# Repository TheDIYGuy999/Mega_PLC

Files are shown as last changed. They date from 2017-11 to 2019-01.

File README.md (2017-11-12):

# This is an Arduino based, modular Industrial PLC

## I have designed this PLC back in 2016. It is currently in use in an industrial screw tightening robot:
- 4 stepper motors for X, Y, Z axes and for screw tightening
- Matrix keyboard
- I2C LCD
- Digital I/O in use for pneumatic screw feeding system, buttons and reference switches

## Features:
- Works wit an Arduino MEGA or DUE
- DO board with 16 24V, 500mA PNP digital outputs, optoinsulated, short circuit protected @ about 900mA
- DI board with 16 24V PNP digital inputs, optoinsulated
- Stepper board for 4 stepper motors, torque adjustable via PWM
- Slot for communication board (I2C, CAN, SPI, 2x Serial)
- Slot for analog board (Analog in, PWM, DAC, I2C)

## This repo contains:
- Eagle schematics
- Eagle board files
- PDF schematics
- The analog and communication boards were made out of perfboard and are NOT included. Maybe someone other is interested in adding them.

## Pictures:
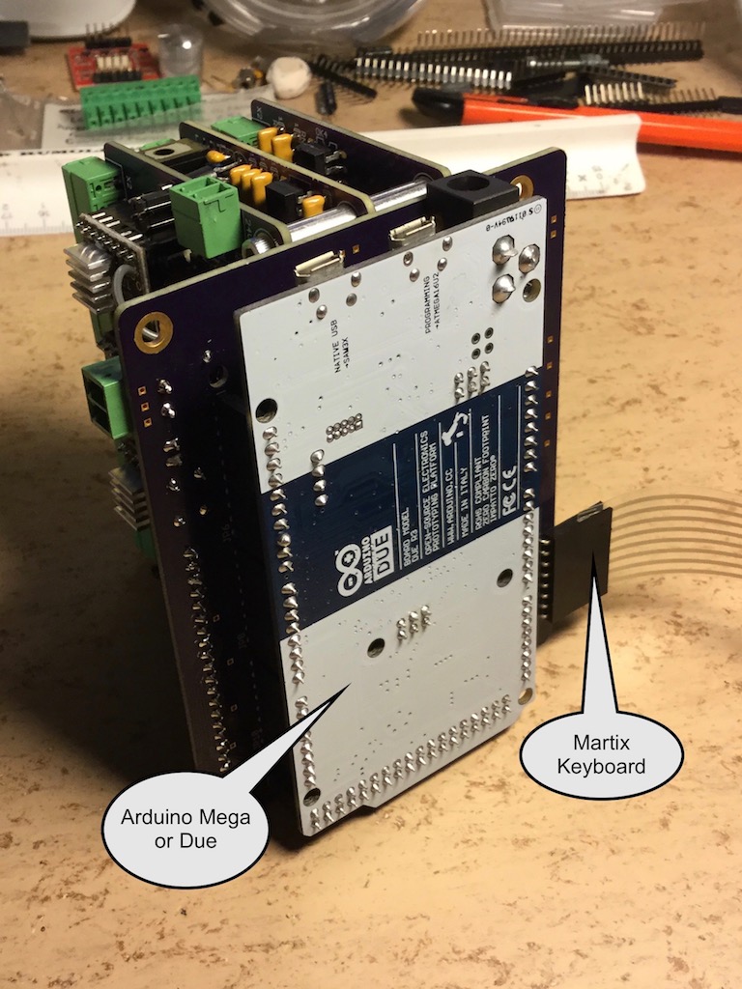
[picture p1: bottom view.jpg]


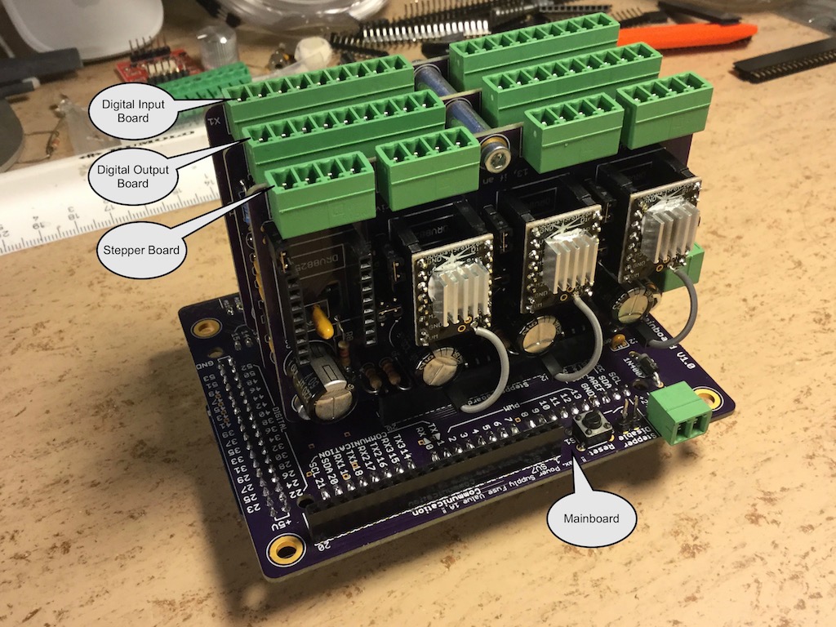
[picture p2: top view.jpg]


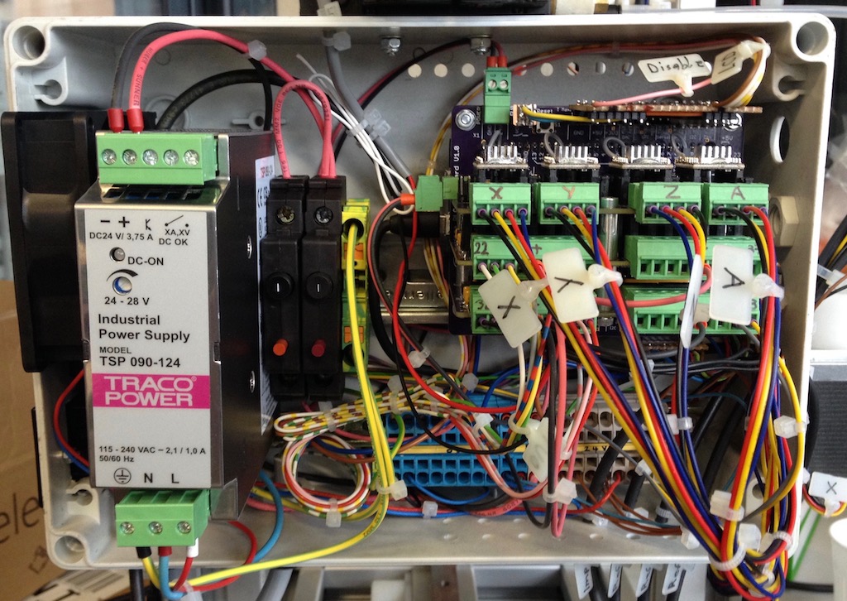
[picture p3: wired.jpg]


## Videos:
- I/O boards: https://www.youtube.com/watch?v=W2pYYh6aUXc
- First tepper tests: https://www.youtube.com/watch?v=gJDdZBuH5Kc

(c) 2016  TheDIYGuy999

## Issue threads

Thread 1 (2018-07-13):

Thyristor BT169 in Digital Output Circuit

rjtphate7, 2018-07-13:
Hey TheDIYGuy999,
The purpose of thyristor BT169 in digital output circuit is quite unclear to me, can you explain?
I have simulated and found it ON irrespective of input to optocoupler

TheDIYGuy999, 2018-07-14:
It does the output short circuit protection, which is triggered at about 0.9A.
The nominal output current is 0.5A

rjtphate7, 2018-07-16:
Any suggestions in case I wish to increase the nominal output current to 2 A?

TheDIYGuy999, 2018-07-16:
0.5A is standard for PLC digital outputs. If you want more, I recommend to use a relay, which is controlled by the PLC output.

rjtphate7, 2018-07-17:
**Thanks for the suggestion**

Closed 2018-07-17.

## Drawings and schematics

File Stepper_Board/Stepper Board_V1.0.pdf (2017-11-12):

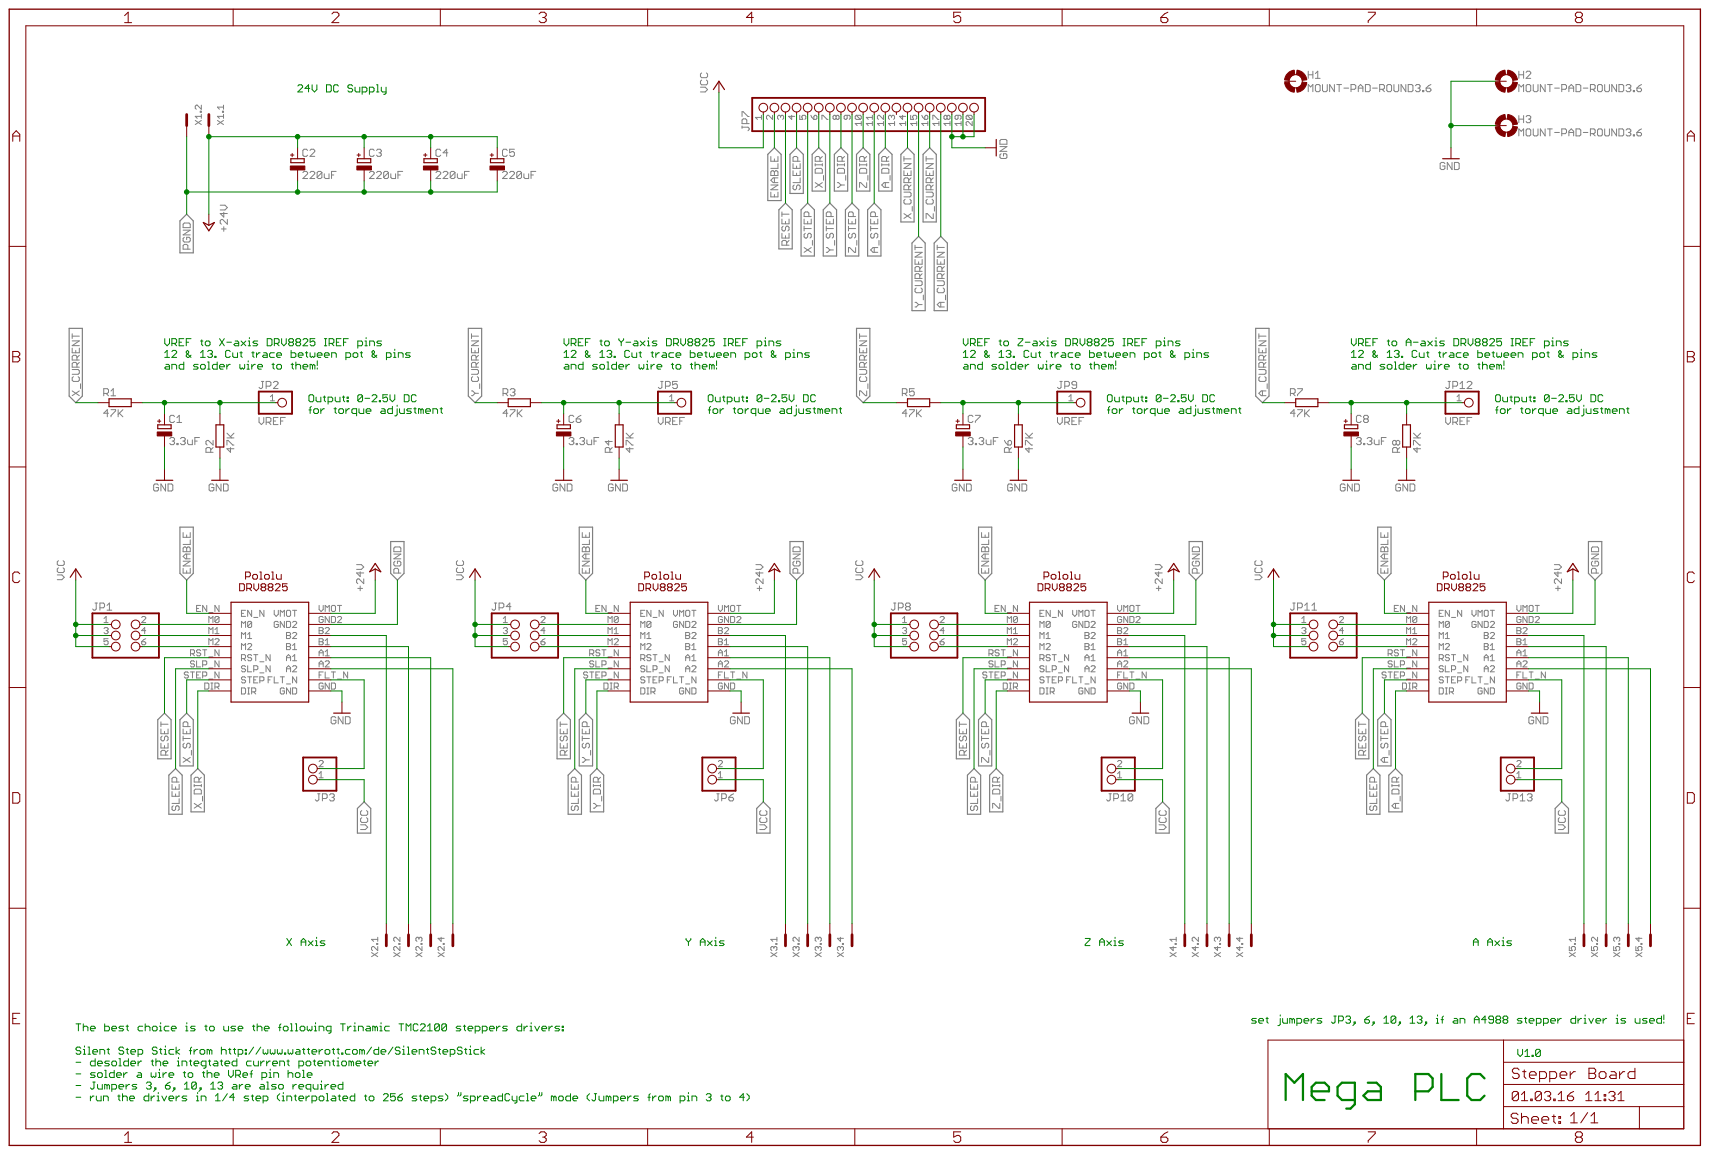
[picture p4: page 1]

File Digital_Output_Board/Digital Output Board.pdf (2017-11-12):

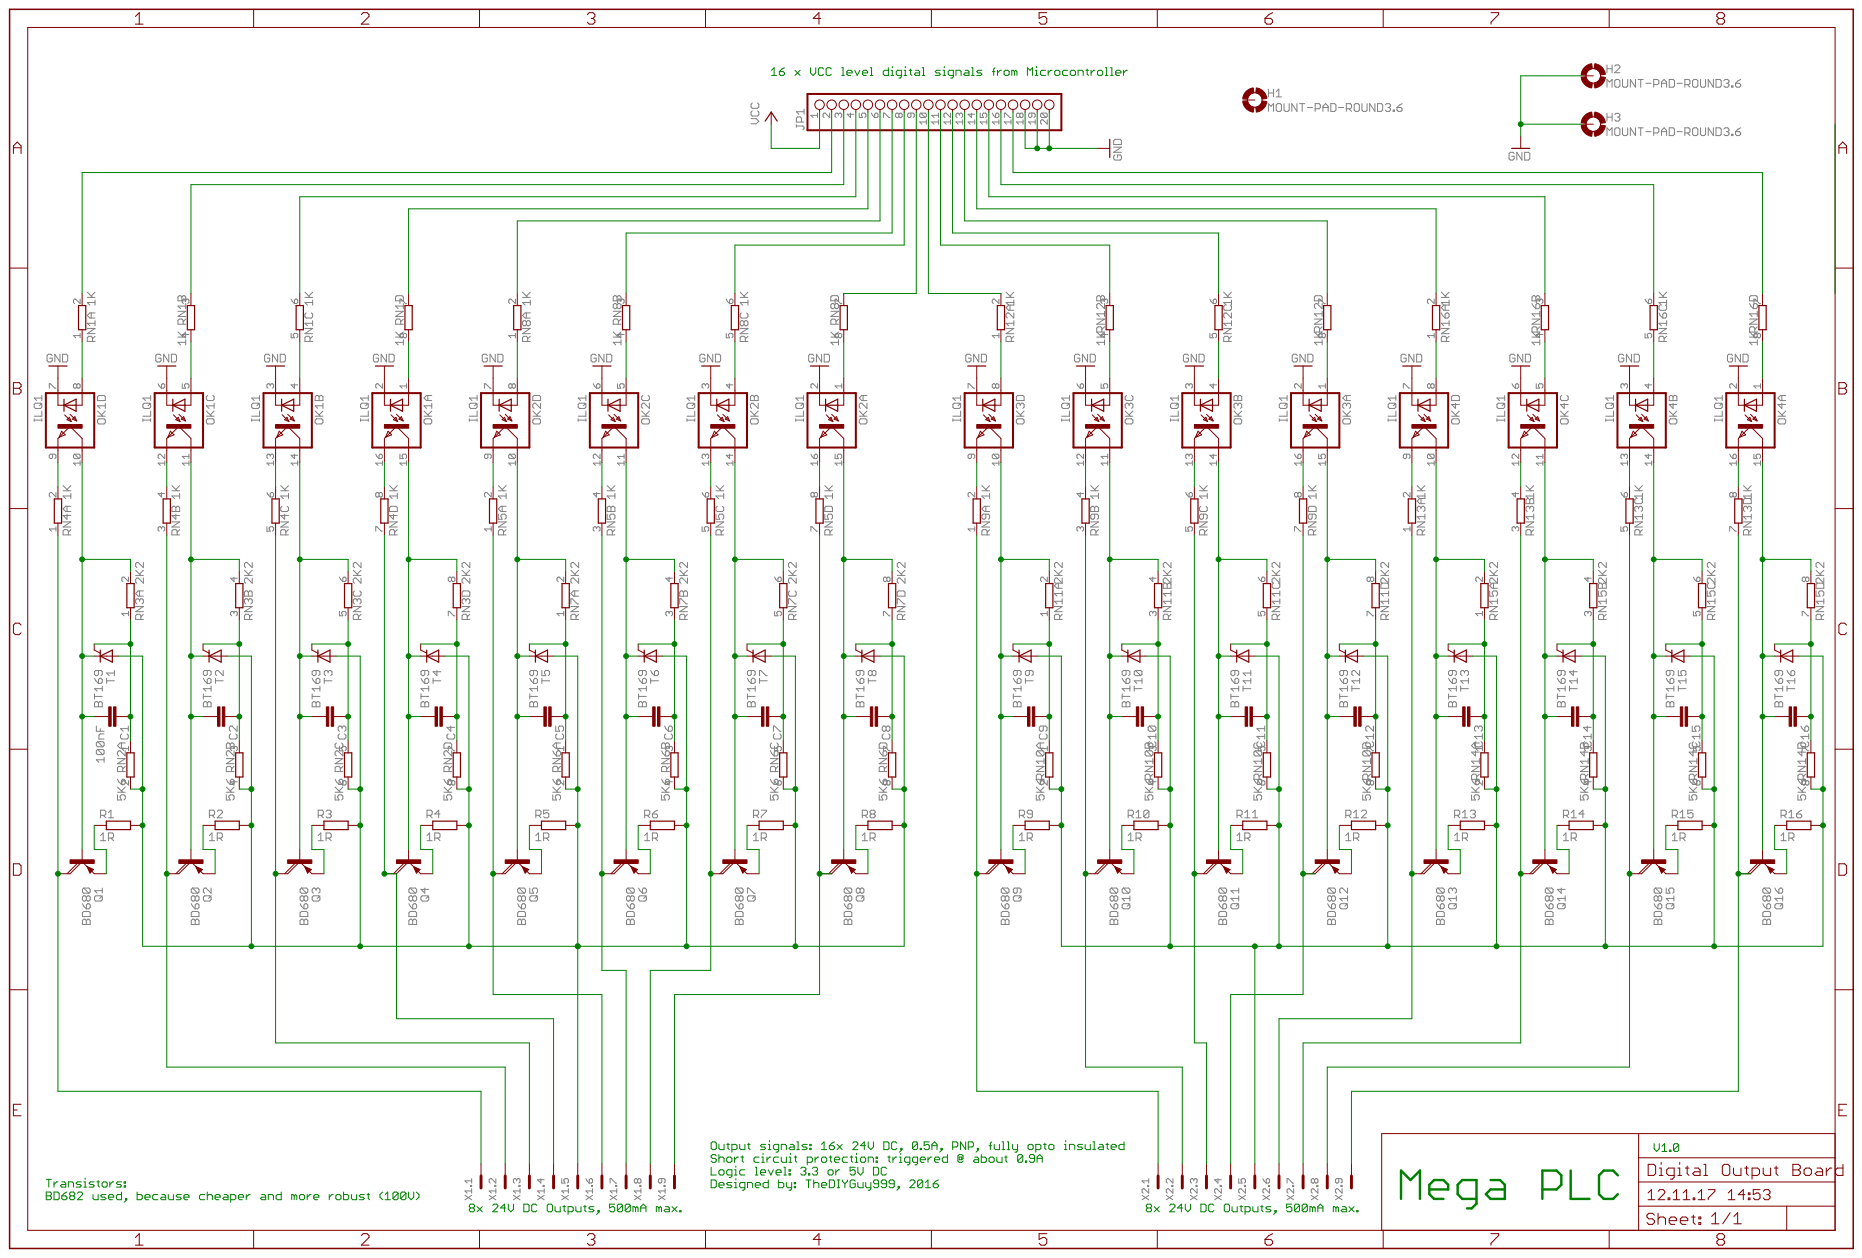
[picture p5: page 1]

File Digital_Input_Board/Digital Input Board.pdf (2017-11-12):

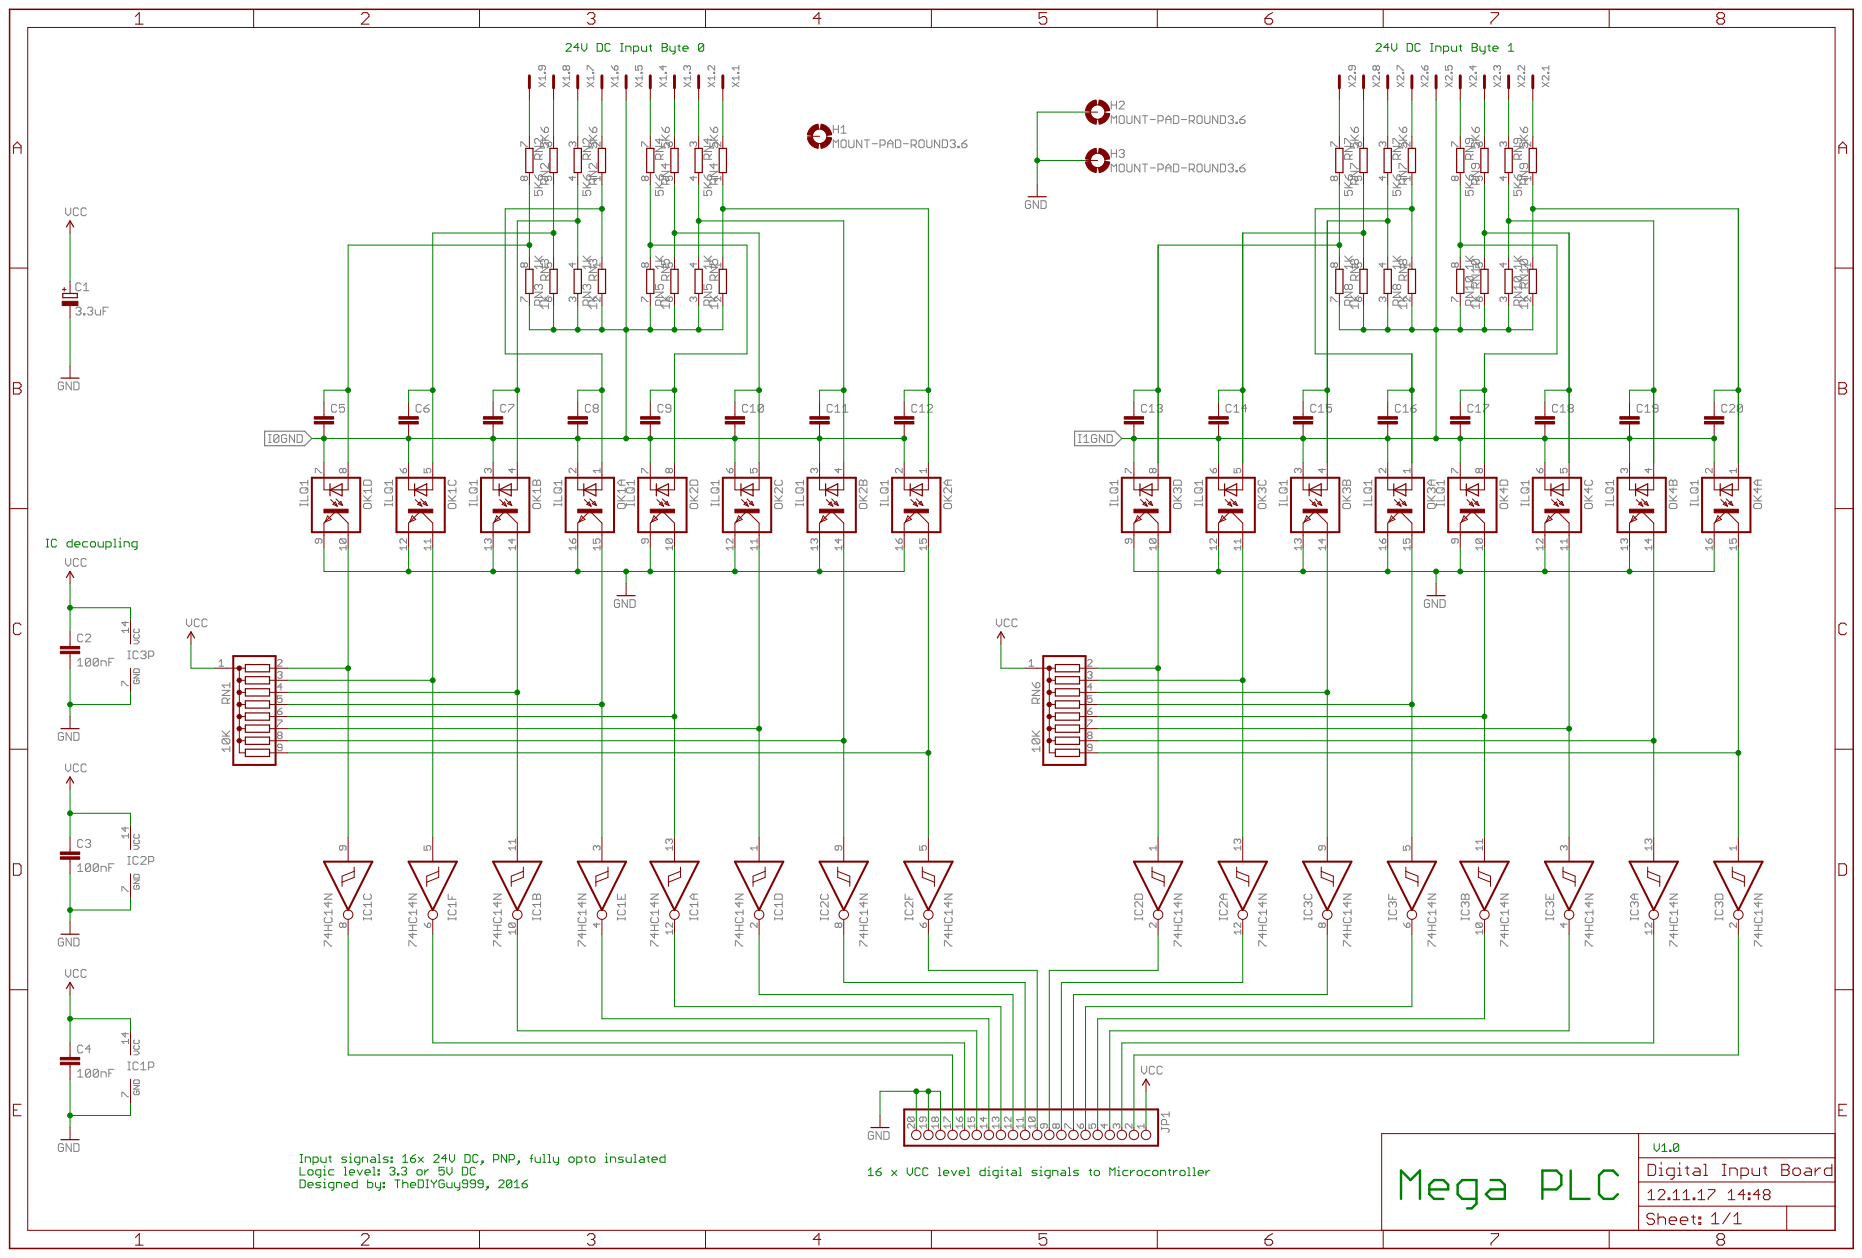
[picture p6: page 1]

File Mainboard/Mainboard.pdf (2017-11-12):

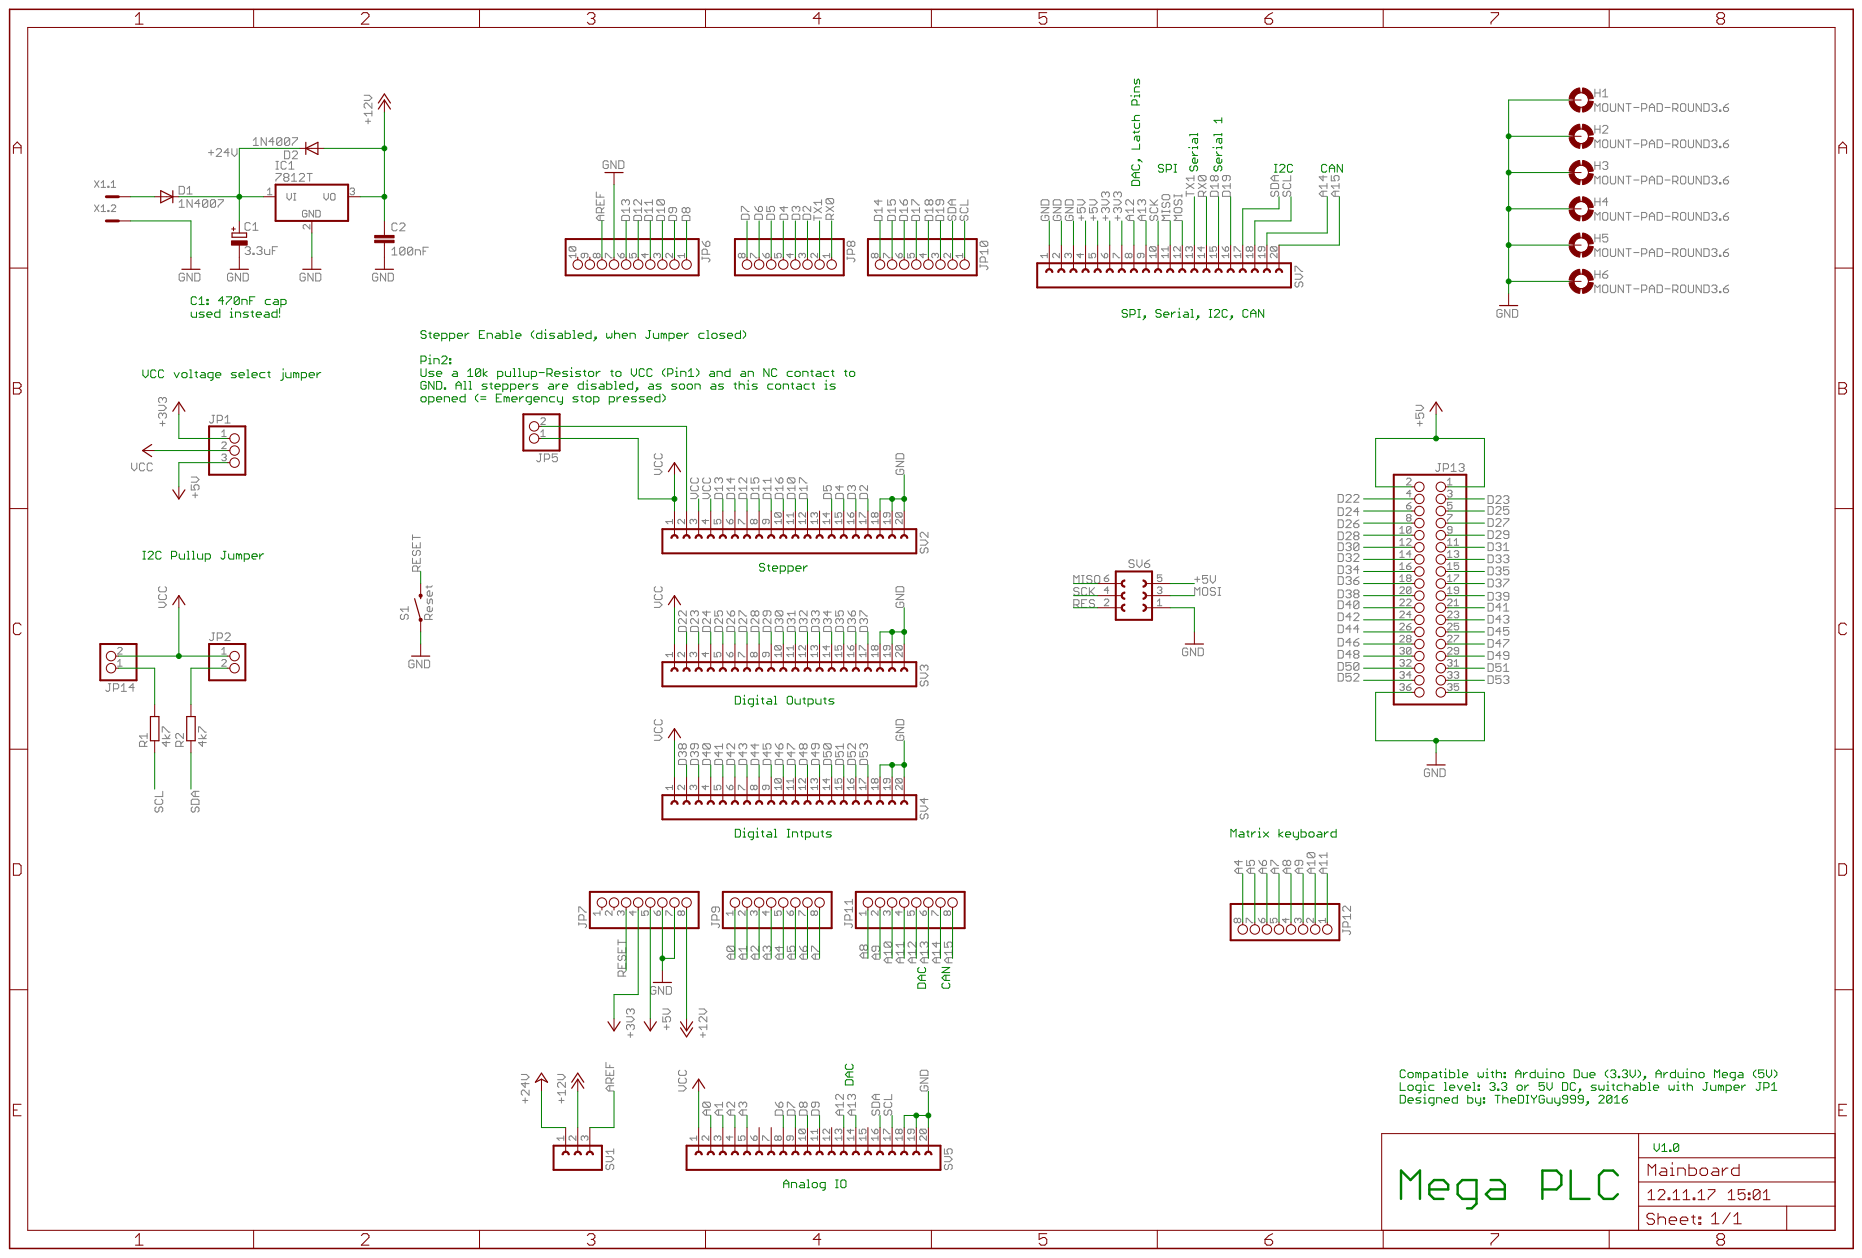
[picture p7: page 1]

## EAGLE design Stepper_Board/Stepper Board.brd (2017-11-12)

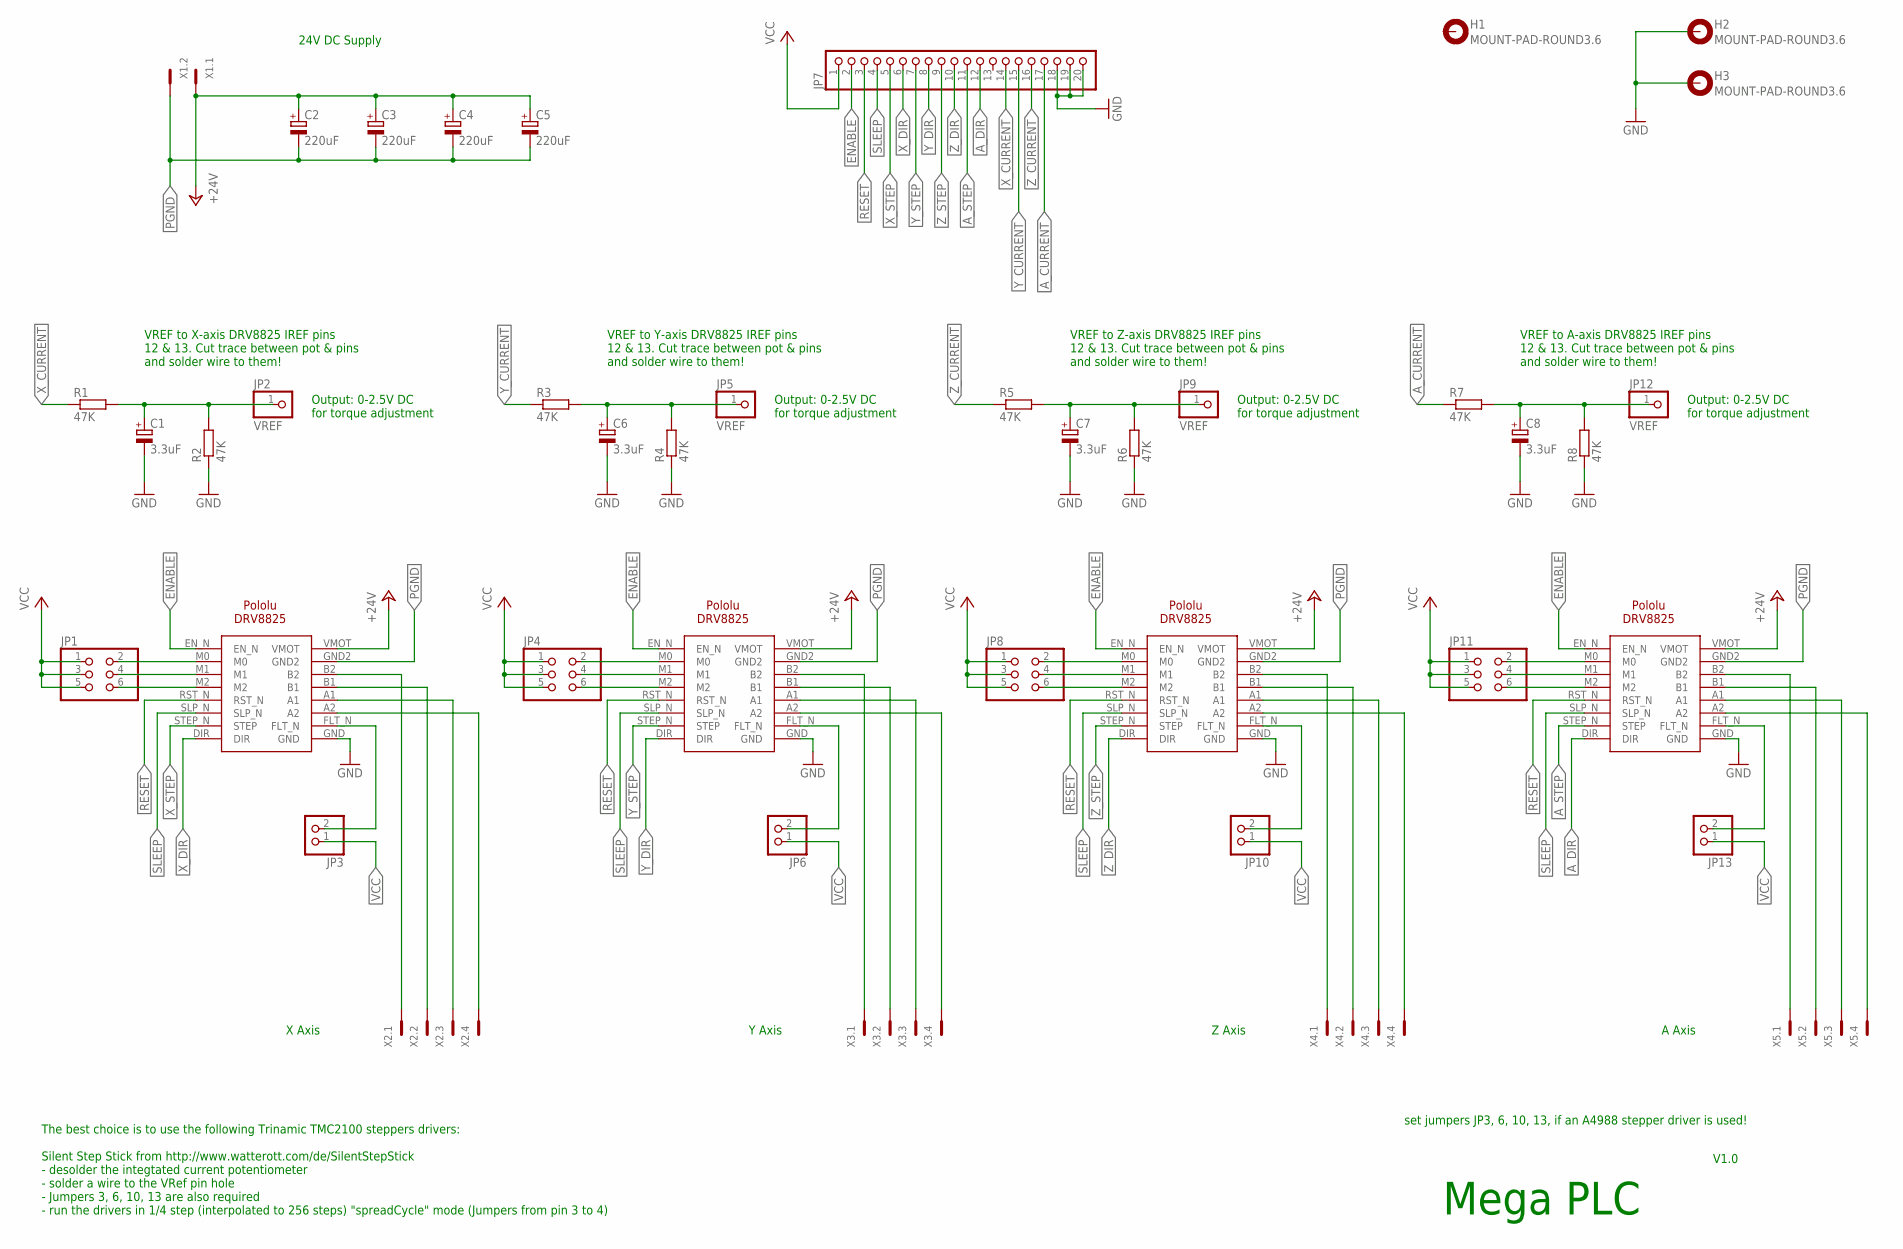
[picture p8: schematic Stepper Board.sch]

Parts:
C1, C6, C7, C8: 3.3uF; B45181A
C2, C3, C4, C5: 220uF; E5-10,5
H1, H2, H3: MOUNT-PAD-ROUND3.6; 3,6-PAD
JP1, JP4, JP8, JP11: PINHD-2X3; 2X03
JP2, JP5, JP9, JP12: VREF; 1X01
JP3, JP6, JP10, JP13: PINHD-1X2; 1X02
JP7: PINHD-1X20/90; 1X20/90
R1: 47K; 0204/7
R2, R4, R6, R8: 47K; 0207/15
R3, R5, R7: 47K; 0207/2V
U1, U2, U3, U4: POLOLU-DRV8825
X1: MC2
X2, X3, X4, X5: MC4

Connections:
+24V: C2.+, C3.+, C4.+, C5.+, U1.VMOT, U2.VMOT, U3.VMOT, U4.VMOT, X1.1
A_CURRENT: JP7.17, R7.1
A_DIR: JP7.12, U4.DIR
A_FLT: JP13.2, U4.FLT_N
A_STEP: JP7.11, U4.STEP_N (STEP)
ENABLE: JP7.2, U1.EN_N, U2.EN_N, U3.EN_N, U4.EN_N
GND: C1.-, C6.-, C7.-, C8.-, H2.B3,6, H3.B3,6, JP7.18, JP7.19, JP7.20, R2.1, R4.1, R6.1, R8.1, U1.GND, U2.GND, U3.GND, U4.GND
unnamed: U1.A2, X2.4
unnamed: U1.A1, X2.3
unnamed: JP1.2, U1.M0
unnamed: JP1.4, U1.M1
unnamed: JP1.6, U1.M2
unnamed: U1.B1, X2.2
unnamed: U1.B2, X2.1
unnamed: U2.A2, X3.4
unnamed: U2.A1, X3.3
unnamed: U2.B1, X3.2
unnamed: U2.B2, X3.1
unnamed: U3.A2, X4.4
unnamed: U3.A1, X4.3
unnamed: U3.B1, X4.2
unnamed: U3.B2, X4.1
unnamed: U4.A2, X5.4
unnamed: U4.A1, X5.3
unnamed: U4.B1, X5.2
unnamed: U4.B2, X5.1
unnamed: JP4.2, U2.M0
unnamed: JP4.4, U2.M1
unnamed: JP4.6, U2.M2
unnamed: JP8.2, U3.M0
unnamed: JP8.4, U3.M1
unnamed: JP8.6, U3.M2
unnamed: JP11.2, U4.M0
unnamed: JP11.4, U4.M1
unnamed: JP11.6, U4.M2
unnamed: C8.+, JP12.1, R7.2, R8.2
unnamed: C7.+, JP9.1, R5.2, R6.2
unnamed: C6.+, JP5.1, R3.2, R4.2
unnamed: C1.+, JP2.1, R1.2, R2.2
PGND: C2.-, C3.-, C4.-, C5.-, U1.GND2, U2.GND2, U3.GND2, U4.GND2, X1.2
RESET: JP7.3, U1.RST_N, U2.RST_N, U3.RST_N, U4.RST_N
SLEEP: JP7.4, U1.SLP_N, U2.SLP_N, U3.SLP_N, U4.SLP_N
VCC: JP1.1, JP1.3, JP1.5, JP3.1, JP4.1, JP4.3, JP4.5, JP6.1, JP7.1, JP8.1, JP8.3, JP8.5, JP10.1, JP11.1, JP11.3, JP11.5, JP13.1
X_CURRENT: JP7.14, R1.1
X_DIR: JP7.6, U1.DIR
X_FLT: JP3.2, U1.FLT_N
X_STEP: JP7.5, U1.STEP_N (STEP)
Y_CURRENT: JP7.15, R3.1
Y_DIR: JP7.8, U2.DIR
Y_FLT: JP6.2, U2.FLT_N
Y_STEP: JP7.7, U2.STEP_N (STEP)
Z_CURRENT: JP7.16, R5.1
Z_DIR: JP7.10, U3.DIR
Z_FLT: JP10.2, U3.FLT_N
Z_STEP: JP7.9, U3.STEP_N (STEP)

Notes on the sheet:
24V DC Supply
VREF to A-axis DRV8825 IREF pins 12 & 13. Cut trace between pot & pins and solder wire to them!
X Axis
Y Axis
Z Axis
A Axis
Output: 0-2.5V DC for torque adjustment
Mega PLC
set jumpers JP3, 6, 10, 13, if an A4988 stepper driver is used!
VREF to Z-axis DRV8825 IREF pins 12 & 13. Cut trace between pot & pins and solder wire to them!
VREF to Y-axis DRV8825 IREF pins 12 & 13. Cut trace between pot & pins and solder wire to them!
VREF to X-axis DRV8825 IREF pins 12 & 13. Cut trace between pot & pins and solder wire to them!
V1.0
The best choice is to use the following Trinamic TMC2100 steppers drivers: Silent Step Stick from http://www.watterott.com/de/SilentStepStick - desolder the integtated current potentiometer - solder a wire to the VRef pin hole - Jumpers 3, 6, 10, 13 are also required - run the drivers in 1/4 step (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

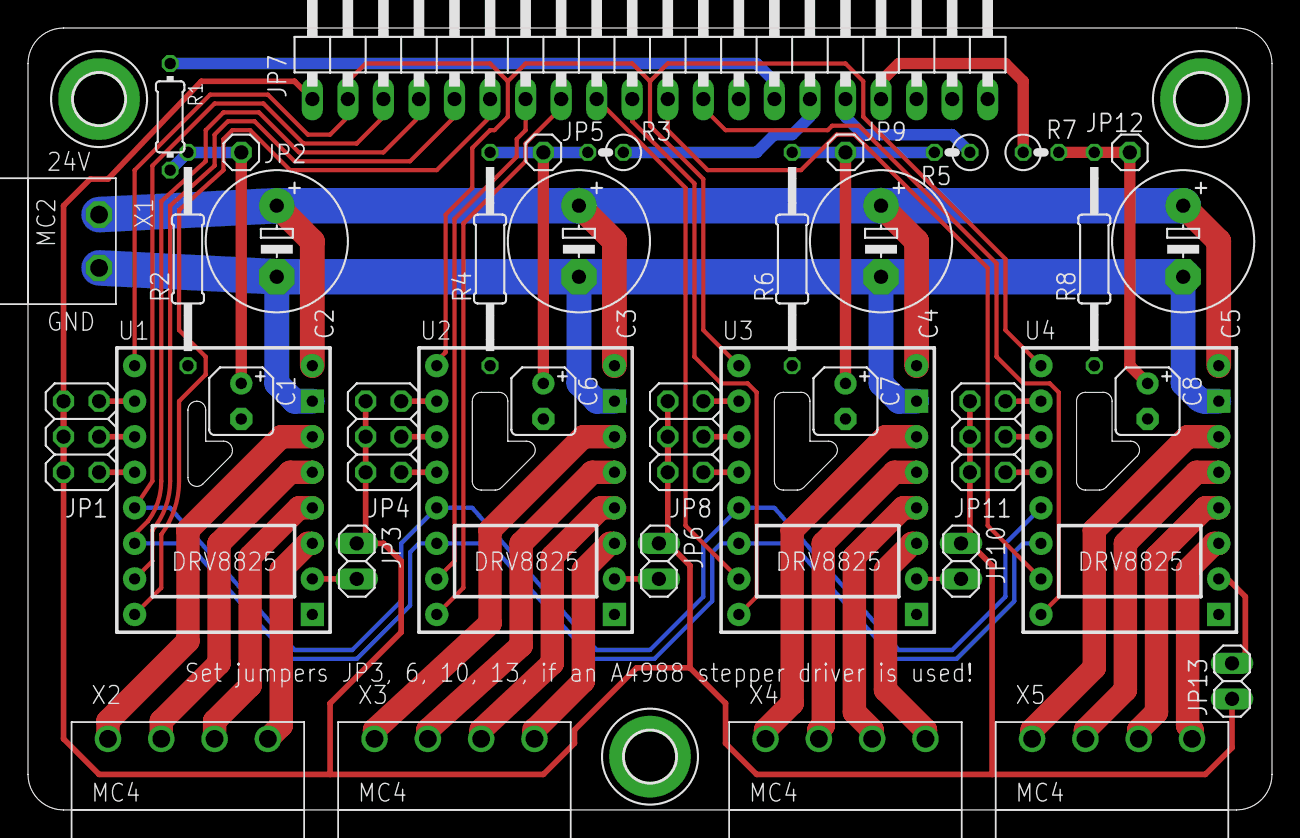
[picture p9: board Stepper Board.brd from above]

Board: 2 copper layers, 88.9 x 55.9 mm, 41 parts (0 on the bottom side), 55 nets.

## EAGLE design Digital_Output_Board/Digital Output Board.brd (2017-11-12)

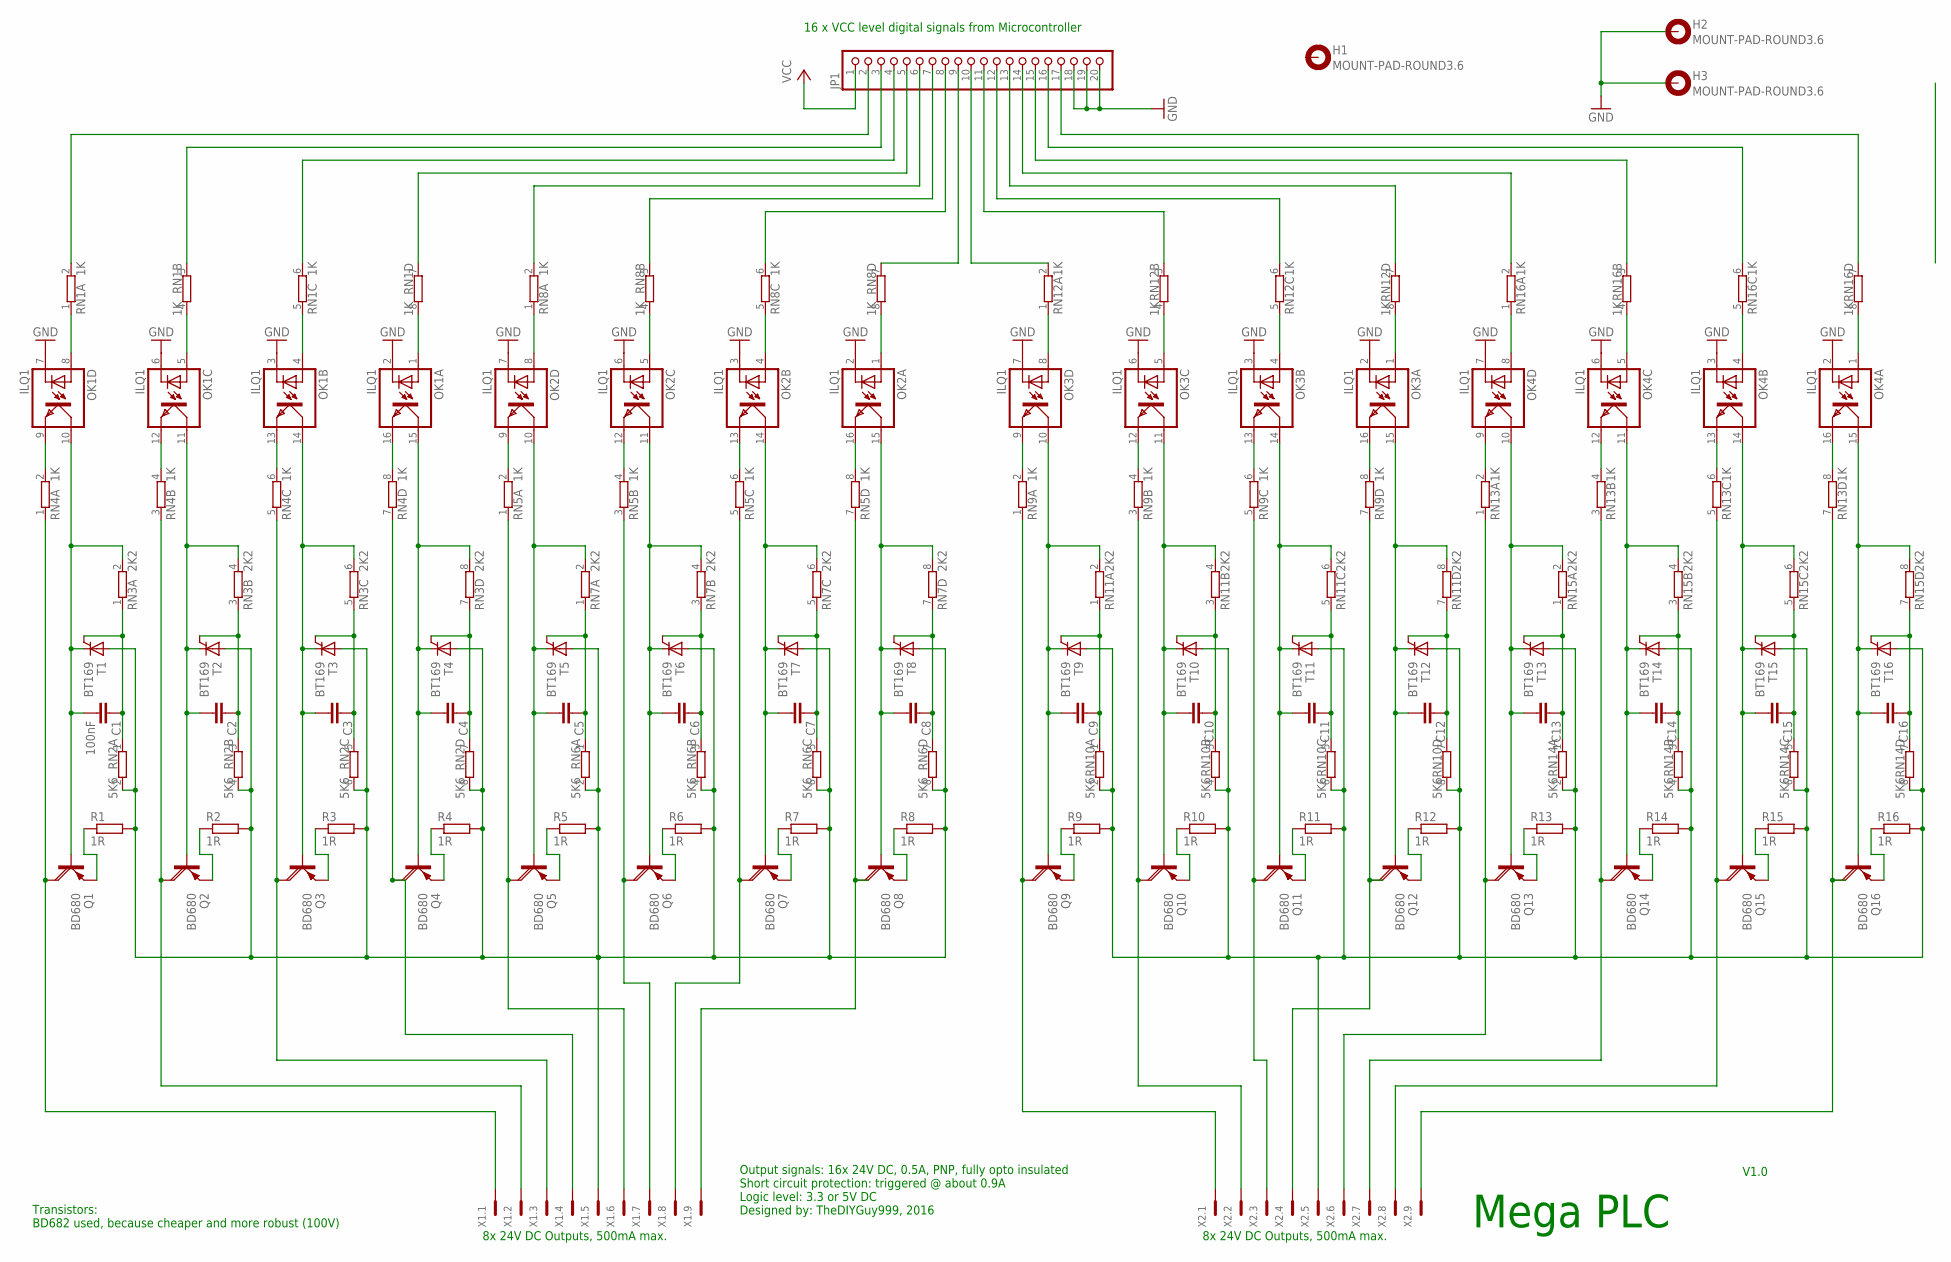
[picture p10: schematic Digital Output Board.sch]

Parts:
C1: 100nF; C025-024X044
C2, C3, C4, C5, C6, C7, C8, C9, C10, C11, C12, C13, C14, C15, C16: C-EU025-024X044; C025-024X044
H1, H2, H3: MOUNT-PAD-ROUND3.6; 3,6-PAD
JP1: PINHD-1X20/90; 1X20/90
OK1, OK2, OK3, OK4: ILQ1; DIL16
Q1, Q2, Q3, Q4, Q5, Q6, Q7, Q8, Q9, Q10, Q11, Q12, Q13, Q14, Q15, Q16: BD680; TO126AV
R1, R2, R3, R4, R5, R6, R7, R8, R9, R10, R11, R12, R13, R14, R15, R16: 1R; 0207/10
RN1, RN4, RN5, RN8, RN9, RN12, RN13, RN16: 1K; SIL8
RN2, RN6, RN10, RN14: 5K6; SIL8
RN3, RN7, RN11, RN15: 2K2; SIL8
T1, T2, T3, T4, T5, T6, T7, T8, T9, T10, T11, T12, T13, T14, T15, T16: BT169; TO92-2
X1, X2: MC9

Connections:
C+1: R1.2, R2.2, R3.2, R4.2, R5.2, R6.2, R7.2, R8.2, RN2.2, RN2.4 (2), RN2.6 (2), RN2.8 (2), RN6.2, RN6.4 (2), RN6.6 (2), RN6.8 (2), T1.A, T2.A, T3.A, T4.A, T5.A, T6.A, T7.A, T8.A, X1.5
C+2: R9.2, R10.2, R11.2, R12.2, R13.2, R14.2, R15.2, R16.2, RN10.2, RN10.4 (2), RN10.6 (2), RN10.8 (2), RN14.2, RN14.4 (2), RN14.6 (2), RN14.8 (2), T9.A, T10.A, T11.A, T12.A, T13.A, T14.A, T15.A, T16.A, X2.5
GND: H2.B3,6, H3.B3,6, JP1.18, JP1.19, JP1.20, OK1.2 (C), OK1.3 (C), OK1.6 (C), OK1.7 (C), OK2.2 (C), OK2.3 (C), OK2.6 (C), OK2.7 (C), OK3.2 (C), OK3.3 (C), OK3.6 (C), OK3.7 (C), OK4.2 (C), OK4.3 (C), OK4.6 (C), OK4.7 (C)
unnamed: Q1.E, R1.1
unnamed: OK1.8 (A), RN1.1
unnamed: OK1.5 (A), RN1.4 (2)
unnamed: OK1.4 (A), RN1.5 (1)
unnamed: OK1.1 (A), RN1.8 (2)
unnamed: JP1.2, RN1.2
unnamed: JP1.3, RN1.3 (1)
unnamed: JP1.4, RN1.6 (2)
unnamed: JP1.5, RN1.7 (1)
unnamed: OK1.9 (EMIT), RN4.2
unnamed: OK1.12 (EMIT), RN4.4 (2)
unnamed: OK1.13 (EMIT), RN4.6 (2)
unnamed: OK1.16 (EMIT), RN4.8 (2)
unnamed: C1.2, OK1.10 (COL), Q1.B, RN3.2, T1.C
unnamed: C1.1, RN2.1, RN3.1, T1.G
unnamed: Q1.C, RN4.1, X1.1
unnamed: Q2.C, RN4.3 (1), X1.2
unnamed: Q3.C, RN4.5 (1), X1.3
unnamed: Q4.C, RN4.7 (1), X1.4
unnamed: C2.2, OK1.11 (COL), Q2.B, RN3.4 (2), T2.C
unnamed: C3.2, OK1.14 (COL), Q3.B, RN3.6 (2), T3.C
unnamed: C4.2, OK1.15 (COL), Q4.B, RN3.8 (2), T4.C
unnamed: Q2.E, R2.1
unnamed: Q3.E, R3.1
unnamed: Q4.E, R4.1
unnamed: C2.1, RN2.3 (1), RN3.3 (1), T2.G
unnamed: C3.1, RN2.5 (1), RN3.5 (1), T3.G
unnamed: C4.1, RN2.7 (1), RN3.7 (1), T4.G
unnamed: JP1.6, RN8.2
unnamed: JP1.7, RN8.3 (1)
unnamed: JP1.8, RN8.6 (2)
unnamed: JP1.9, RN8.7 (1)
unnamed: OK2.8 (A), RN8.1
unnamed: OK2.4 (A), RN8.5 (1)
unnamed: OK2.5 (A), RN8.4 (2)
unnamed: OK2.1 (A), RN8.8 (2)
unnamed: OK2.9 (EMIT), RN5.2
unnamed: OK2.12 (EMIT), RN5.4 (2)
unnamed: OK2.13 (EMIT), RN5.6 (2)
unnamed: OK2.16 (EMIT), RN5.8 (2)
unnamed: C5.1, RN6.1, RN7.1, T5.G
unnamed: Q5.E, R5.1
unnamed: C5.2, OK2.10 (COL), Q5.B, RN7.2, T5.C
unnamed: Q5.C, RN5.1, X1.6
unnamed: Q6.C, RN5.3 (1), X1.7
unnamed: Q7.C, RN5.5 (1), X1.8
unnamed: Q8.C, RN5.7 (1), X1.9
unnamed: C6.2, OK2.11 (COL), Q6.B, RN7.4 (2), T6.C
unnamed: C7.2, OK2.14 (COL), Q7.B, RN7.6 (2), T7.C
unnamed: C8.2, OK2.15 (COL), Q8.B, RN7.8 (2), T8.C
unnamed: Q6.E, R6.1
unnamed: Q7.E, R7.1
unnamed: Q8.E, R8.1
unnamed: C6.1, RN6.3 (1), RN7.3 (1), T6.G
unnamed: C7.1, RN6.5 (1), RN7.5 (1), T7.G
unnamed: C8.1, RN6.7 (1), RN7.7 (1), T8.G
unnamed: OK3.8 (A), RN12.1
unnamed: OK3.4 (A), RN12.5 (1)
unnamed: OK3.5 (A), RN12.4 (2)
unnamed: OK3.1 (A), RN12.8 (2)
unnamed: OK3.9 (EMIT), RN9.2
unnamed: OK3.12 (EMIT), RN9.4 (2)
unnamed: OK3.13 (EMIT), RN9.6 (2)
unnamed: OK3.16 (EMIT), RN9.8 (2)
unnamed: C9.1, RN10.1, RN11.1, T9.G
unnamed: Q9.E, R9.1
unnamed: C9.2, OK3.10 (COL), Q9.B, RN11.2, T9.C
unnamed: Q9.C, RN9.1, X2.1
unnamed: Q10.C, RN9.3 (1), X2.2
unnamed: Q11.C, RN9.5 (1), X2.3
unnamed: Q12.C, RN9.7 (1), X2.4
unnamed: C10.2, OK3.11 (COL), Q10.B, RN11.4 (2), T10.C
unnamed: C11.2, OK3.14 (COL), Q11.B, RN11.6 (2), T11.C
unnamed: C12.2, OK3.15 (COL), Q12.B, RN11.8 (2), T12.C
unnamed: Q10.E, R10.1
unnamed: Q11.E, R11.1
unnamed: Q12.E, R12.1
unnamed: C10.1, RN10.3 (1), RN11.3 (1), T10.G
unnamed: C11.1, RN10.5 (1), RN11.5 (1), T11.G
unnamed: C12.1, RN10.7 (1), RN11.7 (1), T12.G
unnamed: OK4.8 (A), RN16.1
unnamed: OK4.4 (A), RN16.5 (1)
unnamed: OK4.5 (A), RN16.4 (2)
unnamed: OK4.1 (A), RN16.8 (2)
unnamed: OK4.9 (EMIT), RN13.2
unnamed: OK4.12 (EMIT), RN13.4 (2)
unnamed: OK4.13 (EMIT), RN13.6 (2)
unnamed: OK4.16 (EMIT), RN13.8 (2)
unnamed: C13.1, RN14.1, RN15.1, T13.G
unnamed: Q13.E, R13.1
unnamed: C13.2, OK4.10 (COL), Q13.B, RN15.2, T13.C
unnamed: Q13.C, RN13.1, X2.6
unnamed: Q14.C, RN13.3 (1), X2.7
unnamed: Q15.C, RN13.5 (1), X2.8
unnamed: Q16.C, RN13.7 (1), X2.9
unnamed: C14.2, OK4.11 (COL), Q14.B, RN15.4 (2), T14.C
unnamed: C15.2, OK4.14 (COL), Q15.B, RN15.6 (2), T15.C
unnamed: C16.2, OK4.15 (COL), Q16.B, RN15.8 (2), T16.C
unnamed: Q14.E, R14.1
unnamed: Q15.E, R15.1
unnamed: Q16.E, R16.1
unnamed: C14.1, RN14.3 (1), RN15.3 (1), T14.G
unnamed: C15.1, RN14.5 (1), RN15.5 (1), T15.G
unnamed: C16.1, RN14.7 (1), RN15.7 (1), T16.G
unnamed: JP1.10, RN12.2
unnamed: JP1.17, RN16.7 (1)
unnamed: JP1.16, RN16.6 (2)
unnamed: JP1.15, RN16.3 (1)
unnamed: JP1.14, RN16.2
unnamed: JP1.13, RN12.7 (1)
unnamed: JP1.12, RN12.6 (2)
unnamed: JP1.11, RN12.3 (1)
VCC: JP1.1

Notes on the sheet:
16 x VCC level digital signals from Microcontroller
8x 24V DC Outputs, 500mA max.
Transistors: BD682 used, because cheaper and more robust (100V)
Mega PLC
V1.0
Output signals: 16x 24V DC, 0.5A, PNP, fully opto insulated Short circuit protection: triggered @ about 0.9A Logic level: 3.3 or 5V DC Designed by: TheDIYGuy999, 2016

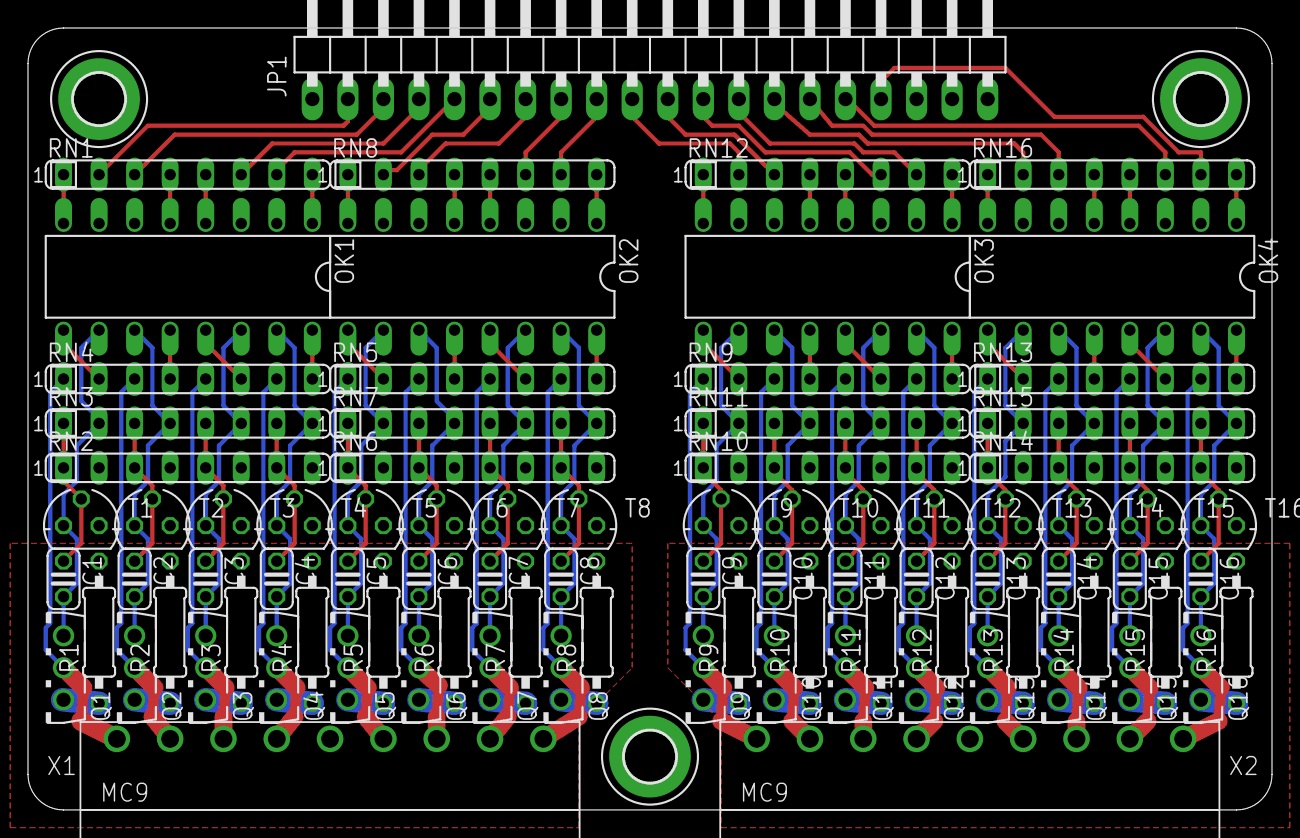
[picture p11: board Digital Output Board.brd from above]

Board: 2 copper layers, 88.9 x 55.9 mm, 90 parts (0 on the bottom side), 115 nets.

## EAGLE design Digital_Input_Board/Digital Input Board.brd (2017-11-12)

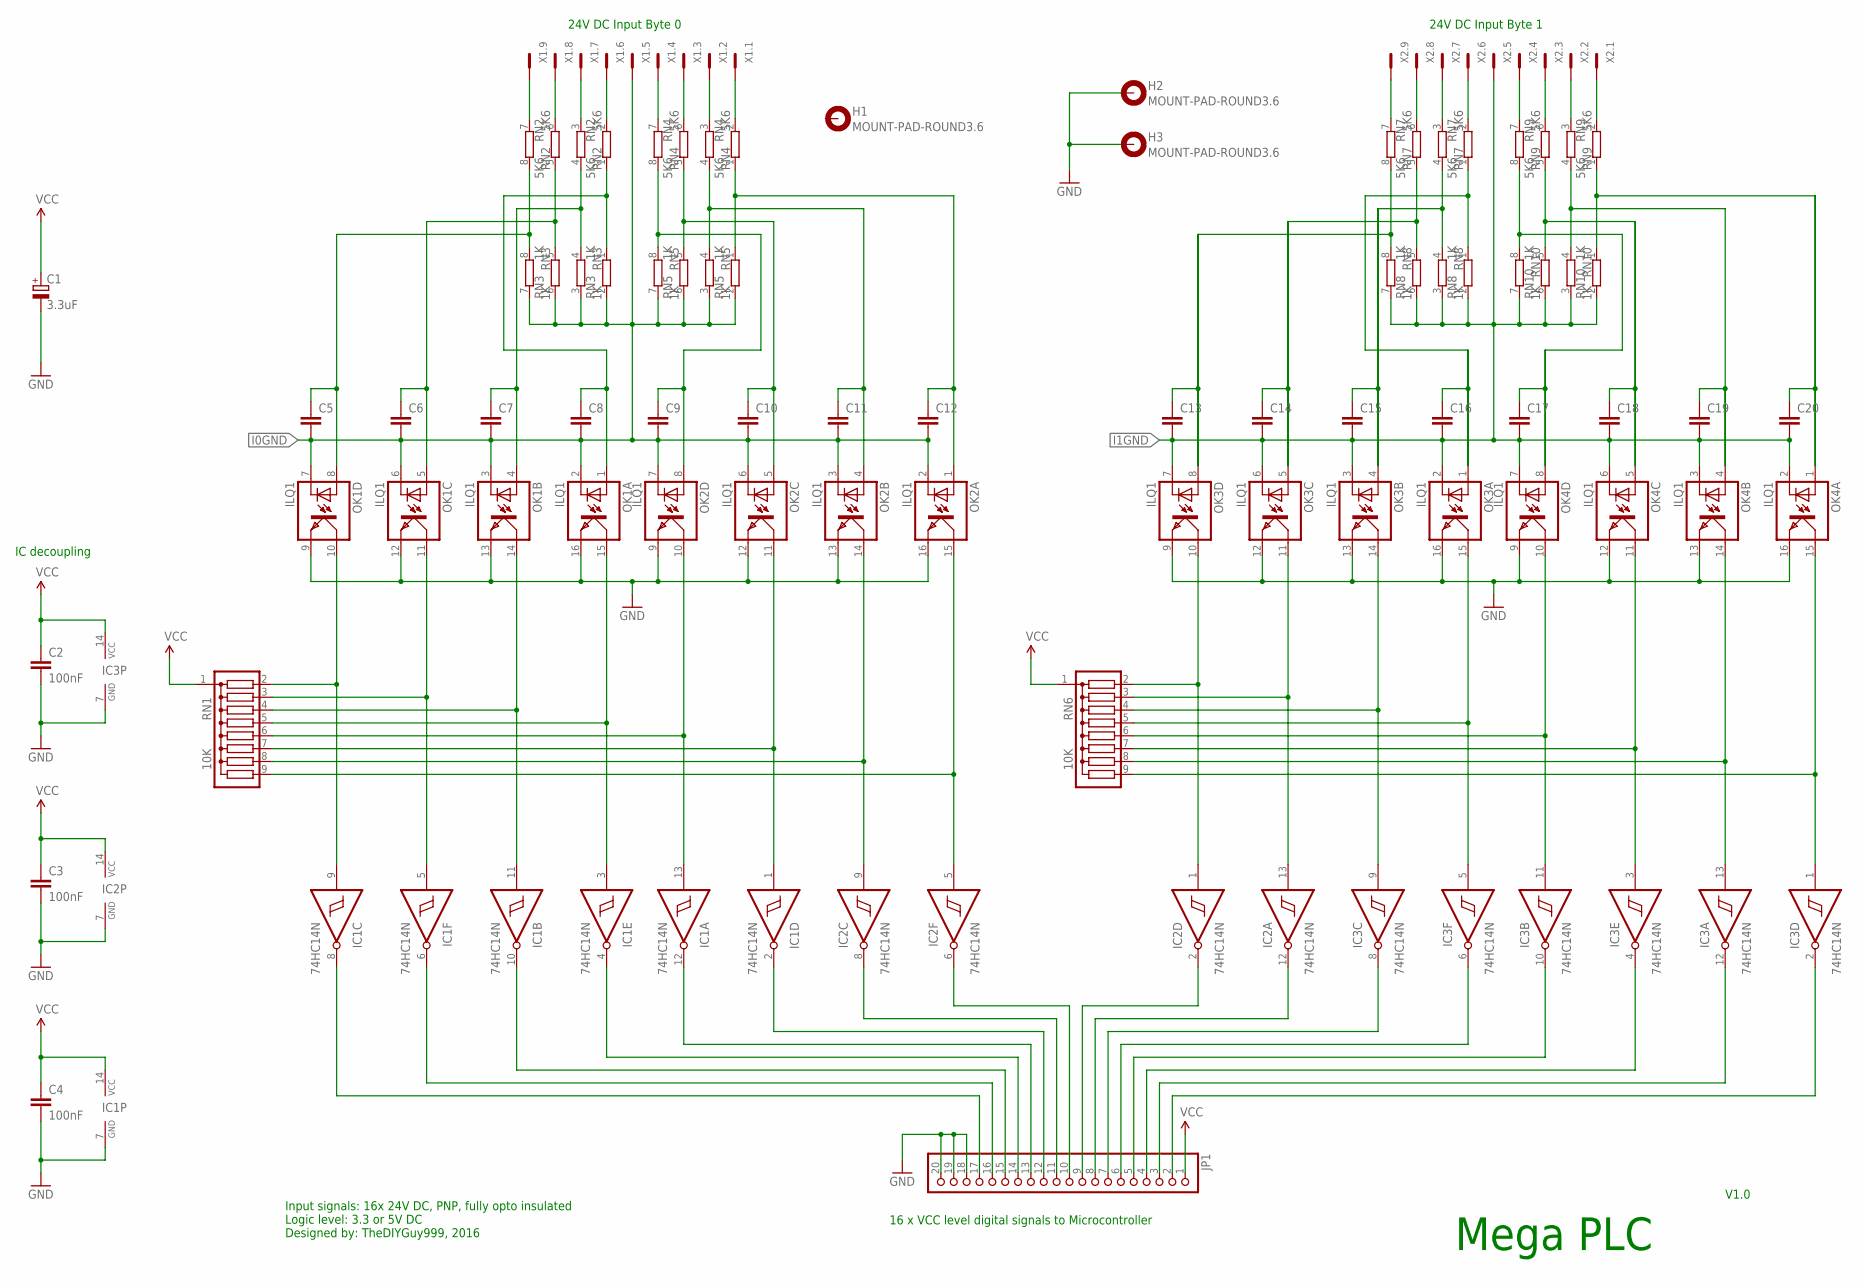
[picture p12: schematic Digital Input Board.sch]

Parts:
C1: 3.3uF; B45181A
C2, C3, C4: 100nF; C025-024X044
C5, C6, C7, C8, C9, C10, C11, C12, C13, C14, C15, C16, C17, C18, C19, C20: C-EUC0805K; C0805K
H1, H2, H3: MOUNT-PAD-ROUND3.6; 3,6-PAD
IC1, IC2, IC3: 74HC14N; DIL14
JP1: PINHD-1X20/90; 1X20/90
OK1, OK2, OK3, OK4: ILQ1; DIL16
RN1, RN6: 10K; SIL9
RN2, RN4, RN7, RN9: 5K6; SIL8
RN3, RN5, RN8, RN10: 1K; SIL8
X1, X2: MC9

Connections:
GND: C1.-, C2.2, C3.2, C4.2, H2.B3,6, H3.B3,6, IC1.7 (GND), IC2.7 (GND), IC3.7 (GND), JP1.18, JP1.19, JP1.20, OK1.9 (EMIT), OK1.12 (EMIT), OK1.13 (EMIT), OK1.16 (EMIT), OK2.9 (EMIT), OK2.12 (EMIT), OK2.13 (EMIT), OK2.16 (EMIT), OK3.9 (EMIT), OK3.12 (EMIT), OK3.13 (EMIT), OK3.16 (EMIT), OK4.9 (EMIT), OK4.12 (EMIT), OK4.13 (EMIT), OK4.16 (EMIT)
I0GND: C5.2, C6.2, C7.2, C8.2, C9.2, C10.2, C11.2, C12.2, OK1.2 (C), OK1.3 (C), OK1.6 (C), OK1.7 (C), OK2.2 (C), OK2.3 (C), OK2.6 (C), OK2.7 (C), RN3.2, RN3.3 (1), RN3.6 (2), RN3.7 (1), RN5.2, RN5.3 (1), RN5.6 (2), RN5.7 (1), X1.5
I1GND: C13.2, C14.2, C15.2, C16.2, C17.2, C18.2, C19.2, C20.2, OK3.2 (C), OK3.3 (C), OK3.6 (C), OK3.7 (C), OK4.2 (C), OK4.3 (C), OK4.6 (C), OK4.7 (C), RN8.2, RN8.3 (1), RN8.6 (2), RN8.7 (1), RN10.2, RN10.3 (1), RN10.6 (2), RN10.7 (1), X2.5
unnamed: RN9.7 (1), X2.4
unnamed: RN9.6 (2), X2.3
unnamed: RN9.3 (1), X2.2
unnamed: RN9.2, X2.1
unnamed: C20.1, OK4.1 (A), RN9.1, RN10.1
unnamed: C19.1, OK4.4 (A), RN9.4 (2), RN10.4 (2)
unnamed: C18.1, OK4.5 (A), RN9.5 (1), RN10.5 (1)
unnamed: C17.1, OK4.8 (A), RN9.8 (2), RN10.8 (2)
unnamed: IC3.1 (I), OK4.15 (COL), RN6.9
unnamed: IC3.13 (I), OK4.14 (COL), RN6.8
unnamed: IC3.3 (I), OK4.11 (COL), RN6.7
unnamed: RN7.2, X2.6
unnamed: IC2.13 (I), OK3.11 (COL), RN6.3
unnamed: RN7.7 (1), X2.9
unnamed: IC3.11 (I), OK4.10 (COL), RN6.6
unnamed: RN7.6 (2), X2.8
unnamed: RN7.3 (1), X2.7
unnamed: C16.1, OK3.1 (A), RN7.1, RN8.1
unnamed: C15.1, OK3.4 (A), RN7.4 (2), RN8.4 (2)
unnamed: C14.1, OK3.5 (A), RN7.5 (1), RN8.5 (1)
unnamed: C13.1, OK3.8 (A), RN7.8 (2), RN8.8 (2)
unnamed: IC3.5 (I), OK3.15 (COL), RN6.5
unnamed: IC3.9 (I), OK3.14 (COL), RN6.4
unnamed: C12.1, OK2.1 (A), RN4.1, RN5.1
unnamed: C11.1, OK2.4 (A), RN4.4 (2), RN5.4 (2)
unnamed: C10.1, OK2.5 (A), RN4.5 (1), RN5.5 (1)
unnamed: C9.1, OK2.8 (A), RN4.8 (2), RN5.8 (2)
unnamed: RN4.7 (1), X1.4
unnamed: RN4.6 (2), X1.3
unnamed: RN4.3 (1), X1.2
unnamed: RN4.2, X1.1
unnamed: IC2.1 (I), OK3.10 (COL), RN6.2
unnamed: IC2.5 (I), OK2.15 (COL), RN1.9
unnamed: IC2.9 (I), OK2.14 (COL), RN1.8
unnamed: IC1.1 (I), OK2.11 (COL), RN1.7
unnamed: RN2.2, X1.6
unnamed: RN2.6 (2), X1.8
unnamed: RN2.7 (1), X1.9
unnamed: RN2.3 (1), X1.7
unnamed: C8.1, OK1.1 (A), RN2.1, RN3.1
unnamed: C7.1, OK1.4 (A), RN2.4 (2), RN3.4 (2)
unnamed: C6.1, OK1.5 (A), RN2.5 (1), RN3.5 (1)
unnamed: C5.1, OK1.8 (A), RN2.8 (2), RN3.8 (2)
unnamed: IC1.13 (I), OK2.10 (COL), RN1.6
unnamed: IC1.3 (I), OK1.15 (COL), RN1.5
unnamed: IC1.11 (I), OK1.14 (COL), RN1.4
unnamed: IC1.5 (I), OK1.11 (COL), RN1.3
unnamed: IC1.9 (I), OK1.10 (COL), RN1.2
unnamed: IC3.2 (O), JP1.2
unnamed: IC3.12 (O), JP1.3
unnamed: IC3.4 (O), JP1.4
unnamed: IC3.10 (O), JP1.5
unnamed: IC3.6 (O), JP1.6
unnamed: IC3.8 (O), JP1.7
unnamed: IC2.12 (O), JP1.8
unnamed: IC2.2 (O), JP1.9
unnamed: IC2.6 (O), JP1.10
unnamed: IC2.8 (O), JP1.11
unnamed: IC1.2 (O), JP1.12
unnamed: IC1.12 (O), JP1.13
unnamed: IC1.4 (O), JP1.14
unnamed: IC1.10 (O), JP1.15
unnamed: IC1.6 (O), JP1.16
unnamed: IC1.8 (O), JP1.17
VCC: C1.+, C2.1, C3.1, C4.1, IC1.14 (VCC), IC2.14 (VCC), IC3.14 (VCC), JP1.1, RN1.1, RN6.1

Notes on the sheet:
Mega PLC
24V DC Input Byte 0
24V DC Input Byte 1
16 x VCC level digital signals to Microcontroller
IC decoupling
V1.0
Input signals: 16x 24V DC, PNP, fully opto insulated Logic level: 3.3 or 5V DC Designed by: TheDIYGuy999, 2016

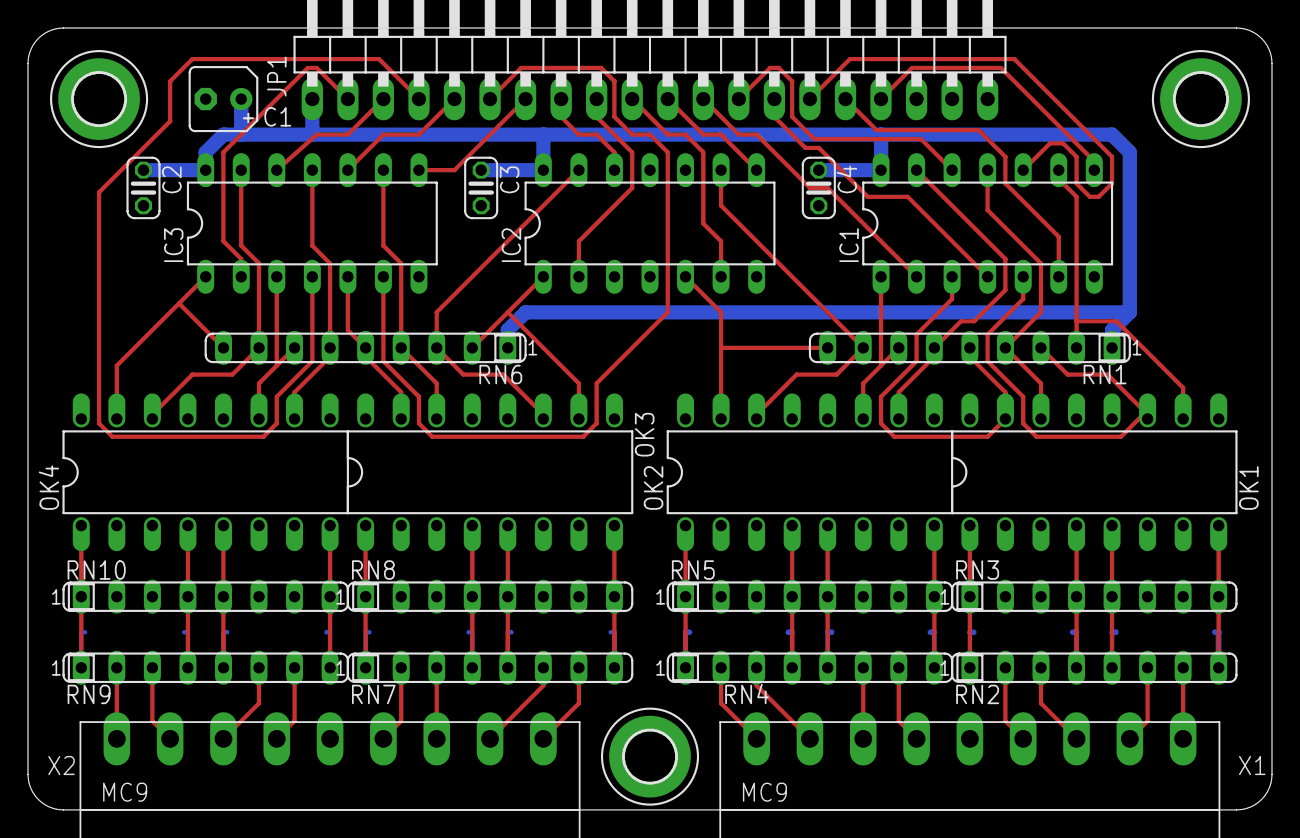
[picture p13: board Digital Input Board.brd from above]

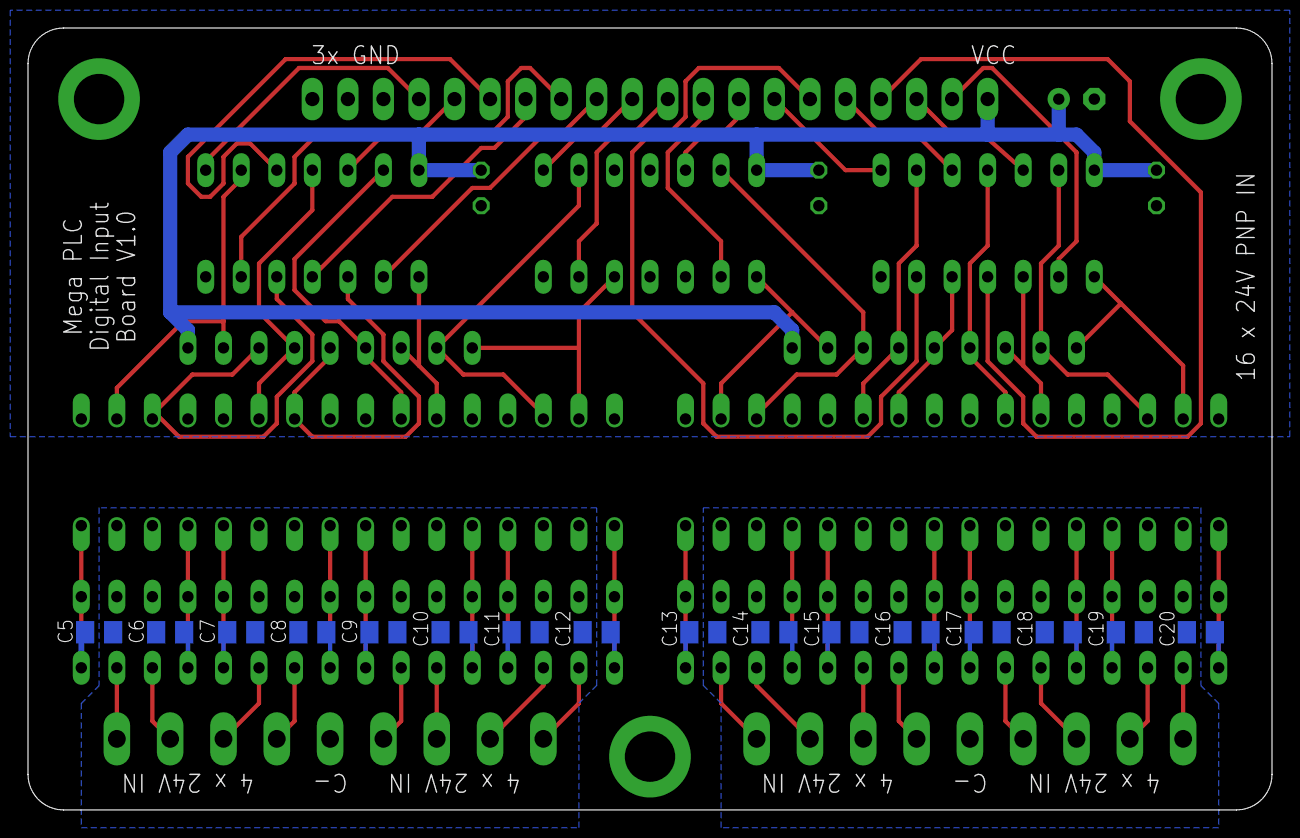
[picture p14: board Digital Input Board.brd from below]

Board: 2 copper layers, 88.9 x 55.9 mm, 43 parts (16 on the bottom side), 68 nets.

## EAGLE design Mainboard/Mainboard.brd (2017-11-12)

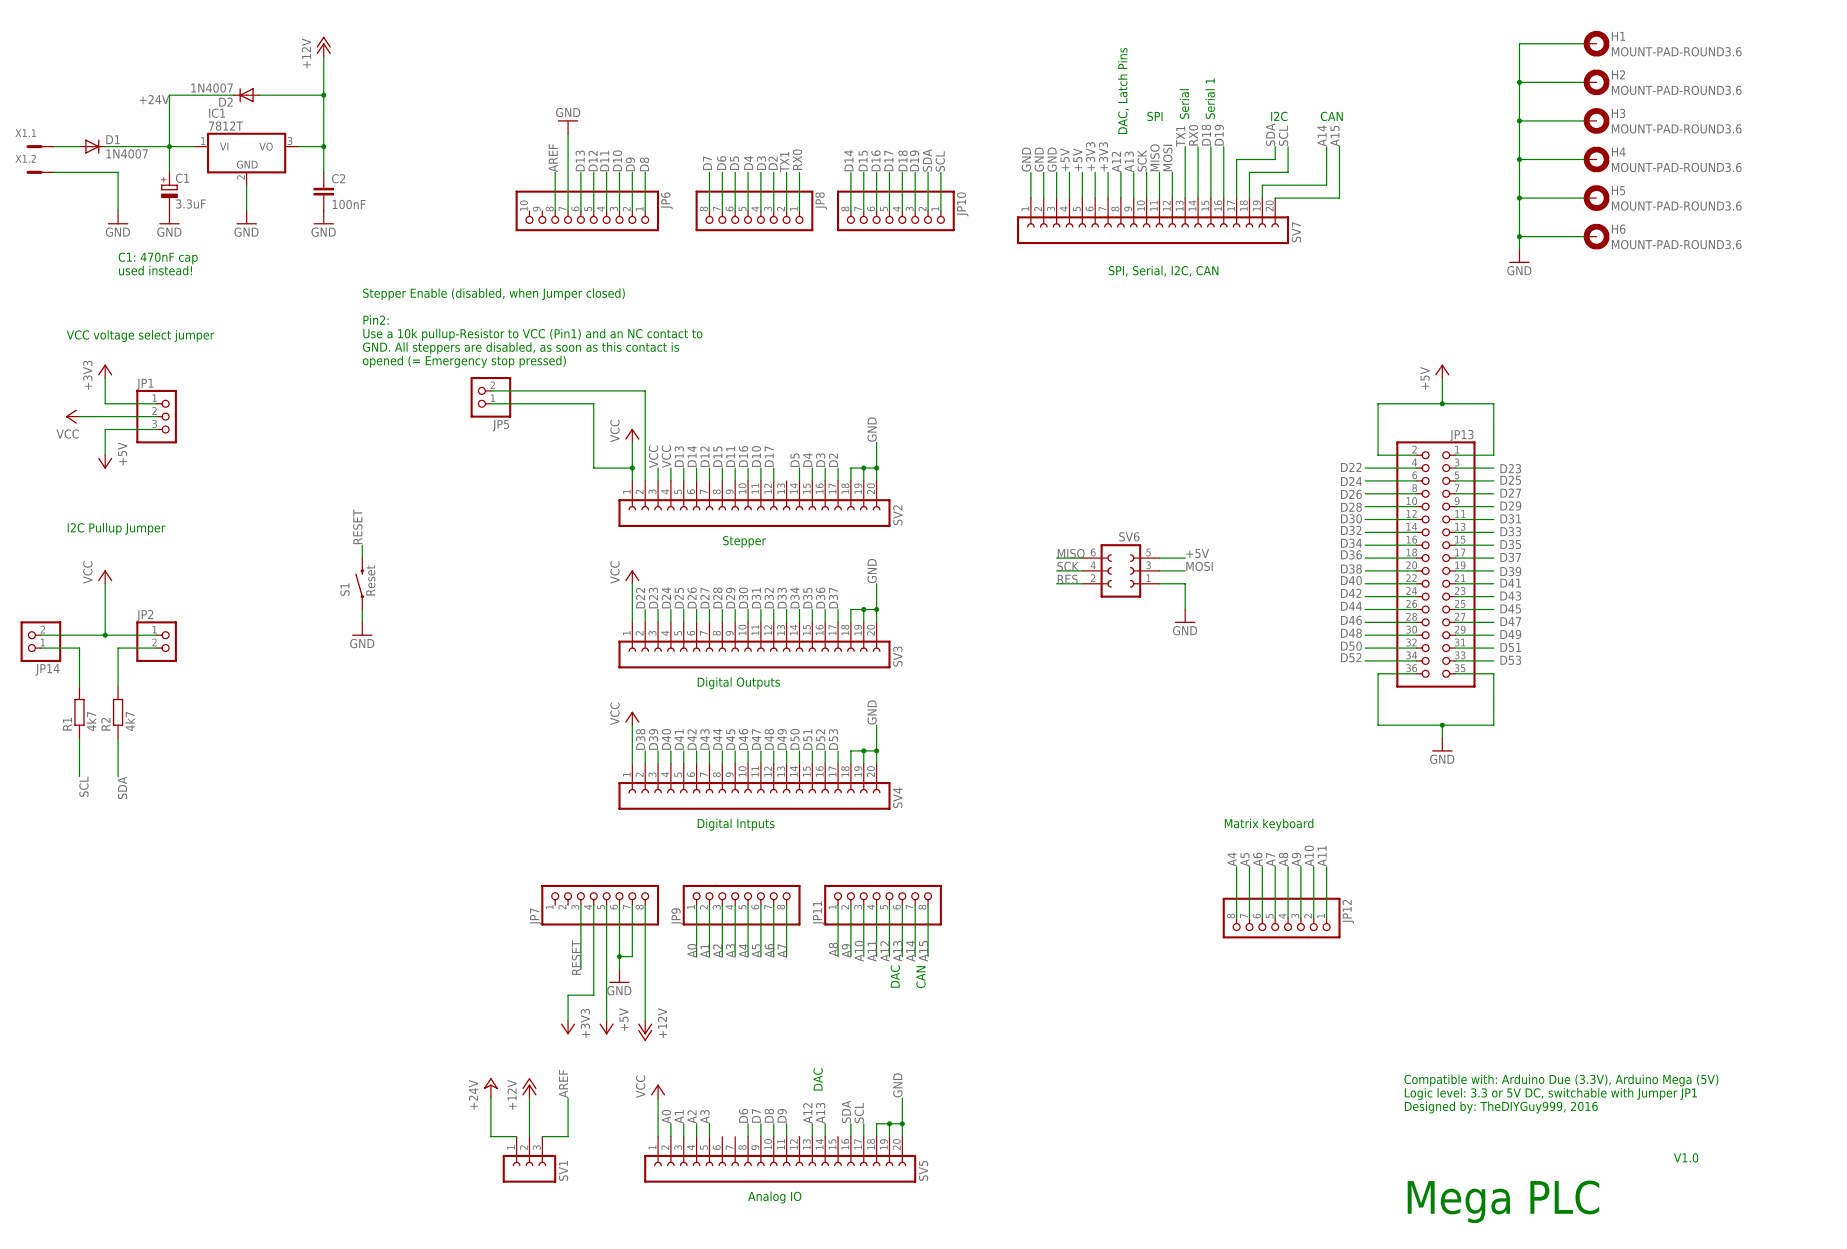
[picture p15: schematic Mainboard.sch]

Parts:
C1: 3.3uF; B45181A
C2: 100nF; C025-024X044
D1, D2: 1N4007; DO41-10
H1, H2, H3, H4, H5, H6: MOUNT-PAD-ROUND3.6; 3,6-PAD
IC1: 7812T; TO220H
JP1: PINHD-1X3; 1X03
JP2, JP5, JP14: PINHD-1X2; 1X02
JP6: PINHD-1X10; 1X10
JP7, JP8, JP9, JP10, JP11, JP12: PINHD-1X8; 1X08
JP13: PINHD-2X18; 2X18
R1, R2: 4k7; 0207/10
S1: Reset; TACTILE-PTH
SV1: FE03-1
SV2, SV3, SV4, SV5, SV7: FE20-1; FE20
SV6: FE03-2
X1: MC2

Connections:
+3V3: JP1.1, JP7.4, SV7.6, SV7.7
+5V: JP1.3, JP7.5, JP13.1, JP13.2, SV6.5, SV7.4, SV7.5
+12V: C2.1, D2.A, IC1.3 (VO), JP7.8, SV1.2
+24V: C1.+, D1.C, D2.C, IC1.1 (VI), SV1.1
A0: JP9.1, SV5.2
A1: JP9.2, SV5.3
A2: JP9.3, SV5.4
A3: JP9.4, SV5.5
A4: JP9.5, JP12.8
A5: JP9.6, JP12.7
A6: JP9.7, JP12.6
A7: JP9.8, JP12.5
A8: JP11.1, JP12.4
A9: JP11.2, JP12.3
A10: JP11.3, JP12.2
A11: JP11.4, JP12.1
A12: JP11.5, SV5.13, SV7.8
A13: JP11.6, SV5.14, SV7.9
A14: JP11.7, SV7.19
A15: JP11.8, SV7.20
AREF: JP6.8, SV1.3
D2: JP8.3, SV2.17
D3: JP8.4, SV2.16
D4: JP8.5, SV2.15
D5: JP8.6, SV2.14
D6: JP8.7, SV5.8
D7: JP8.8, SV5.9
D8: JP6.1, SV5.10
D9: JP6.2, SV5.11
D10: JP6.3, SV2.11
D11: JP6.4, SV2.9
D12: JP6.5, SV2.7
D13: JP6.6, SV2.5
D14: JP10.8, SV2.6
D15: JP10.7, SV2.8
D16: JP10.6, SV2.10
D17: JP10.5, SV2.12
D18: JP10.4, SV7.15
D19: JP10.3, SV7.16
D22: JP13.4, SV3.2
D23: JP13.3, SV3.3
D24: JP13.6, SV3.4
D25: JP13.5, SV3.5
D26: JP13.8, SV3.6
D27: JP13.7, SV3.7
D28: JP13.10, SV3.8
D29: JP13.9, SV3.9
D30: JP13.12, SV3.10
D31: JP13.11, SV3.11
D32: JP13.14, SV3.12
D33: JP13.13, SV3.13
D34: JP13.16, SV3.14
D35: JP13.15, SV3.15
D36: JP13.18, SV3.16
D37: JP13.17, SV3.17
D38: JP13.20, SV4.2
D39: JP13.19, SV4.3
D40: JP13.22, SV4.4
D41: JP13.21, SV4.5
D42: JP13.24, SV4.6
D43: JP13.23, SV4.7
D44: JP13.26, SV4.8
D45: JP13.25, SV4.9
D46: JP13.28, SV4.10
D47: JP13.27, SV4.11
D48: JP13.30, SV4.12
D49: JP13.29, SV4.13
D50: JP13.32, SV4.14
D51: JP13.31, SV4.15
D52: JP13.34, SV4.16
D53: JP13.33, SV4.17
GND: C1.-, C2.2, H1.B3,6, H2.B3,6, H3.B3,6, H4.B3,6, H5.B3,6, H6.B3,6, IC1.2 (GND), JP6.7, JP7.6, JP7.7, JP13.35, JP13.36, S1.1, SV2.18, SV2.19, SV2.20, SV3.18, SV3.19, SV3.20, SV4.18, SV4.19, SV4.20, SV5.18, SV5.19, SV5.20, SV6.1, SV7.1, SV7.2, SV7.3, X1.2
MISO: SV6.6, SV7.11
MOSI: SV6.3, SV7.12
unnamed: JP5.2, SV2.2
unnamed: D1.A, X1.1
RES: SV6.2
RESET: JP7.3, S1.3 (2)
RX0: JP8.1, SV7.14
SCK: SV6.4, SV7.10
SCL: JP10.1, R1.1, SV5.17, SV7.18
SCL_PULLUP: JP14.1, R1.2
SDA: JP10.2, R2.1, SV5.16, SV7.17
SDA_PULLUP: JP2.2, R2.2
TX1: JP8.2, SV7.13
VCC: JP1.2, JP2.1, JP5.1, JP14.2, SV2.1, SV2.3, SV2.4, SV3.1, SV4.1, SV5.1

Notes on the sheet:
Mega PLC
VCC voltage select jumper
I2C Pullup Jumper
Digital Outputs
Digital Intputs
Stepper
CAN
SPI, Serial, I2C, CAN
Analog IO
DAC
Matrix keyboard
I2C
Serial
Serial 1
Stepper Enable (disabled, when Jumper closed) Pin2: Use a 10k pullup-Resistor to VCC (Pin1) and an NC contact to GND. All steppers are disabled, as soon as this contact is opened (= Emergency stop pressed)
SPI
DAC, Latch Pins
V1.0
C1: 470nF cap used instead!
Compatible with: Arduino Due (3.3V), Arduino Mega (5V) Logic level: 3.3 or 5V DC, switchable with Jumper JP1 Designed by: TheDIYGuy999, 2016

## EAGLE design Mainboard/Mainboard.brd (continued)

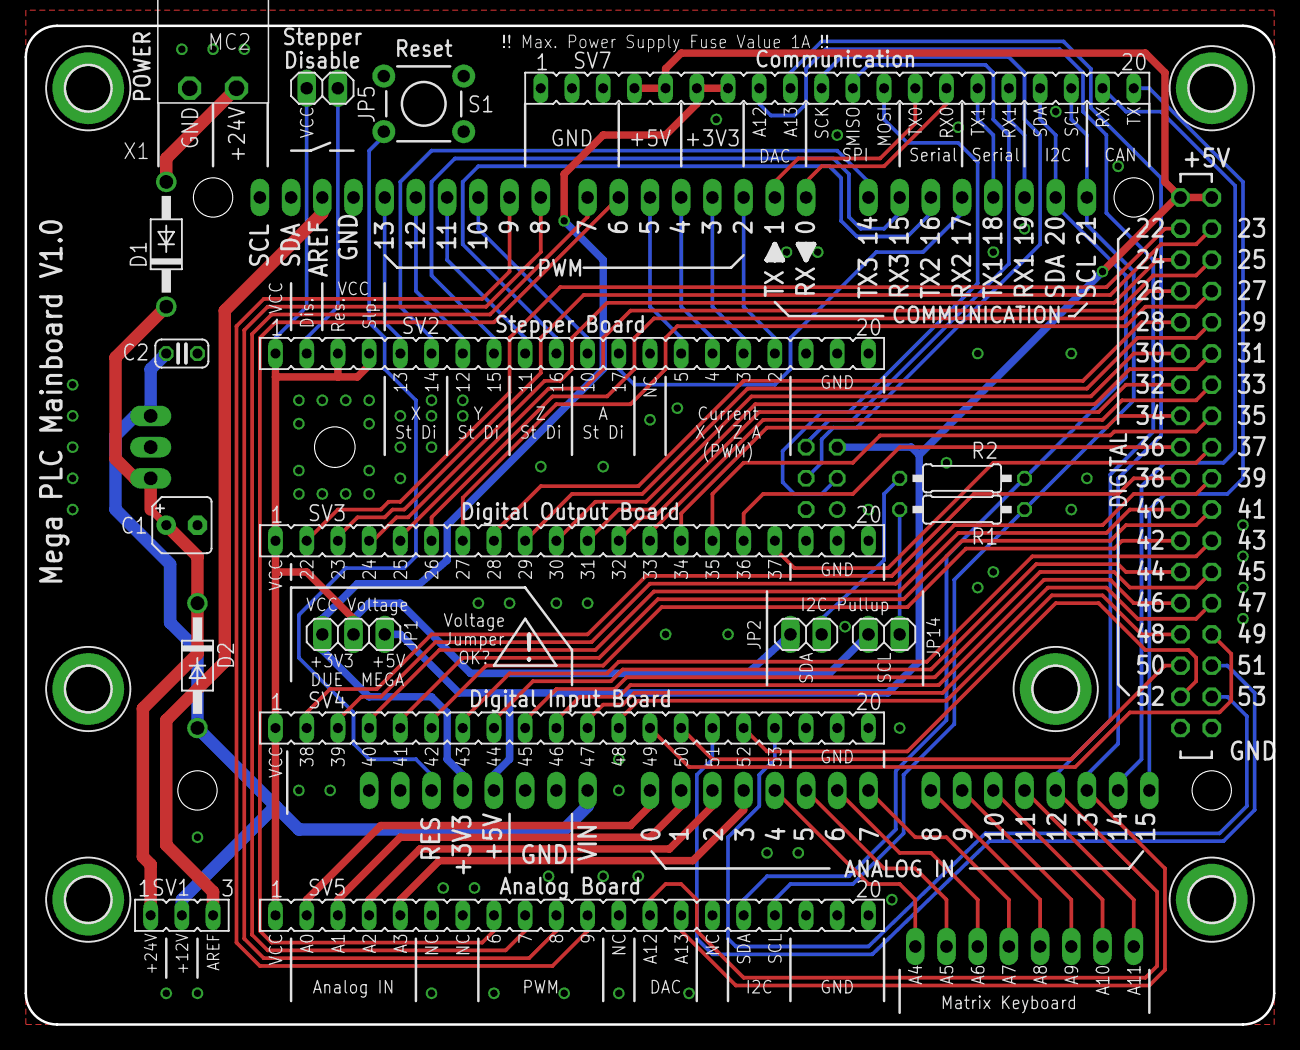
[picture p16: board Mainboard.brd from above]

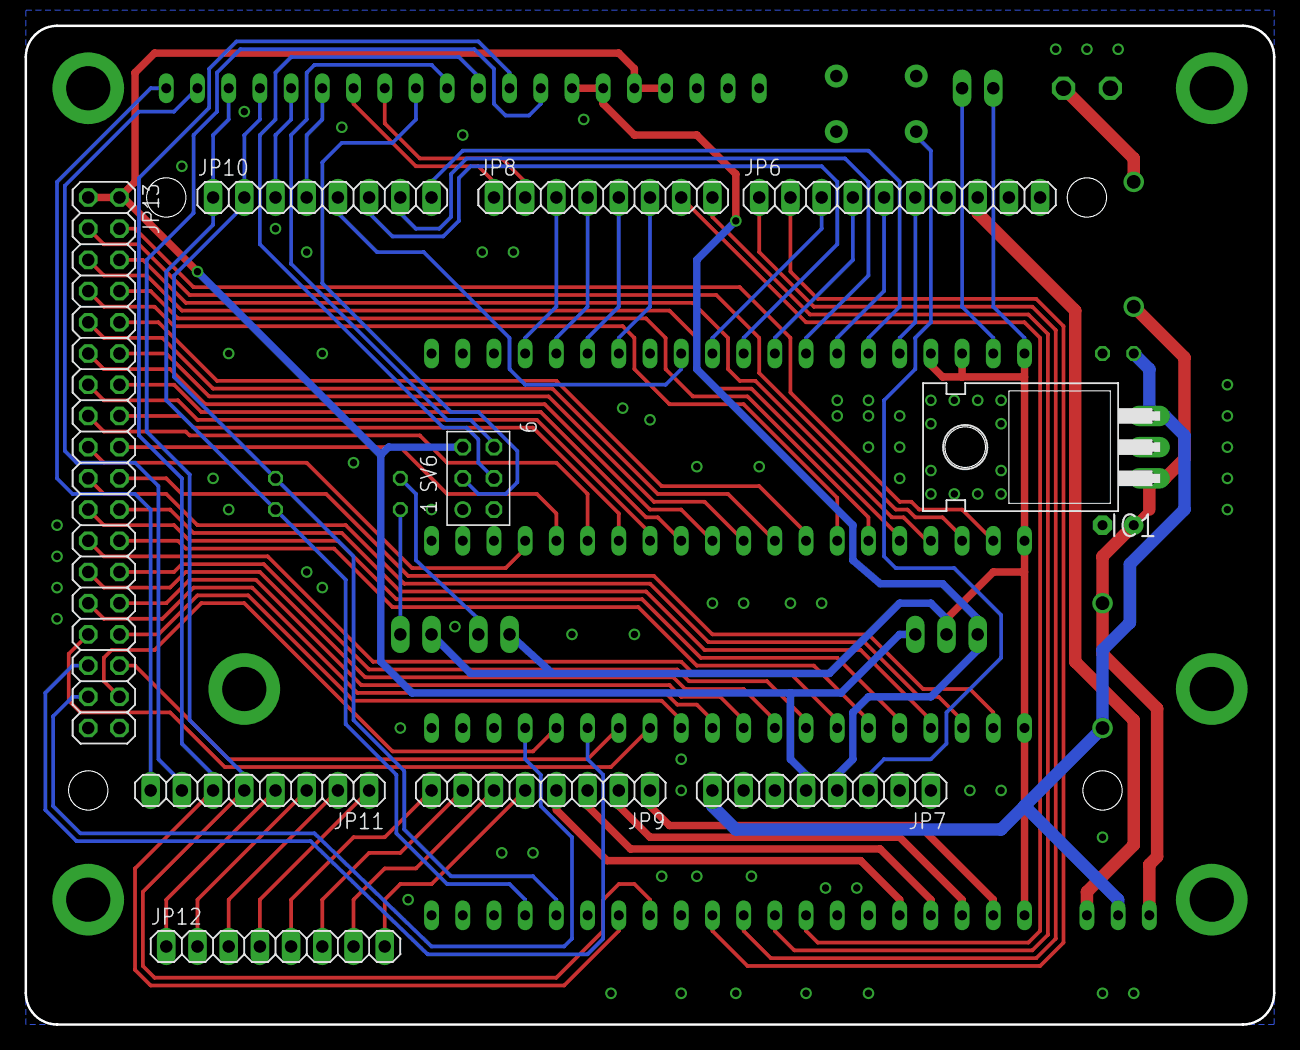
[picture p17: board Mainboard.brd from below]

Board: 2 copper layers, 101.6 x 81.3 mm, 34 parts (10 on the bottom side), 85 nets.

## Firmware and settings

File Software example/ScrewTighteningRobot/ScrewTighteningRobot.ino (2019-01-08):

//
// =======================================================================================================
// PROJECT DESCRIPTION
// =======================================================================================================
//
// Screw tightening robot with 16x2 I2C display, automatic scew feeder

// Arduino Board:         Due
// Mainmoard:             Mega PLC Mainboard V1.0
// Digital input board:   Mega PLC Digital Input Board V1.0
// Digital output board:  Mega PLC Digital Output Board V1.0
// Stepper drivers:       Watterott Silent Step Stick with TMC2100
// Stepper motors:        NEMA 17 "High Torque" from fredee.ch 0.65Nm @ 1.5A, 4V

// Mega PLC supplier:     TheDIYGuy999: https://github.com/TheDIYGuy999/Mega_PLC

//
// =======================================================================================================
// LIBRARIES
// =======================================================================================================
//

// STEPPER
#include <AccelStepper.h> // http://www.airspayce.com/mikem/arduino/AccelStepper/

// DISPLAY
#include <Wire.h> // I2C library
#include <LiquidCrystal_I2C.h> // https://github.com/fdebrabander/Arduino-LiquidCrystal-I2C-library

// KEYPAD
#include <Keypad.h> // http://playground.arduino.cc/Code/Keypad

// SPI BUS FOR SD CARD
#include <SPI.h>
#include <SD.h>

// TIMER
#include <SimpleTimer.h> // https://github.com/jfturcot/SimpleTimer

// Cylinder monitoring
#include "cylinderPositionMonitoring.h"

//
// =======================================================================================================
// BUILD OPTIONS (comment out unneeded options)
// =======================================================================================================
//

//#define DEBUG // if not commented out, Serial.print() is active! For debugging only!!

//
// =======================================================================================================
// PIN ASSIGNMENTS & GLOBAL VARIABLES
// =======================================================================================================
//

//
// Digital 0, 1, Shared as serial pins (Serial1)
// Digital 2 - 13, General Purpose
// Digital 3, 5, 6, 9, 10, 11, and 13 - PWM
// Digital 11 - 13 Excluded on Pro Micro
// Digital 13 has (not Leo) an LED and resistor attached to it
// Digital 14 - 16, Shared with an SPI bus
// Digital 17 - Doubles and RX LED
// Digital Pins can sink 40ma, recommended 470 ohm resistor
// Analog Inputs: A0-A3, Pro Micro excludes A4, A5
// Analog Inputs: A6-A11 (on digital pins 4, 6, 8, 9, 10, and 12)
// Analog Pins can be used as digital ( refer to them as A0, A1, ...)
//

byte startButtonState;

// macro for detection of rising edge and debouncing
/*the state argument (which must be a variable) records the current and the last 3 reads
  by shifting one bit to the left at each read and bitwise anding with 15 (=0b1111).
  If the value is 7(=0b0111) we have one raising edge followed by 3 consecutive 1's.
  That would qualify as a debounced raising edge*/
#define DRE(signal, state) (state=(state<<1)|(signal&1)&15)==7

// LCD Display-------------------------------------------------------------------------

// set the LCD address to 0x27 for a 16 chars and 2 line display
LiquidCrystal_I2C lcd(0x27, 16, 2);

// Keypad------------------------------------------------------------------------------

const byte ROWS = 4; //four rows (4 Zeilen)
const byte COLS = 4; //four columns (4 Spalten)
//define the cymbols on the buttons of the keypads
char keys[ROWS][COLS] = {
  {'1', '2', '3', 'A'},
  {'4', '5', '6', 'B'},
  {'7', '8', '9', 'C'},
  {'*', '0', '#', 'D'}
};
byte rowPins[ROWS] = {A11, A10, A9, A8}; //connect to the row pinouts of the keypad
byte colPins[COLS] = {A7, A6, A5, A4}; //connect to the column pinouts of the keypad

//initialize an instance of class NewKeypad
Keypad customKeypad = Keypad( makeKeymap(keys), rowPins, colPins, ROWS, COLS);
int value = 0;

// Chip select pin for SD card reader-----------------------------------------------------
const int SD_CS = DAC1; // A13 on the mainboard

// General purpose 24V DC Digital Inputs (on the "Digital Input Board")--------------------
const int DI_38_X_REF_SWITCH = 38; // X, Y, Z Reference switches (in parallel)
const int DI_39_Y_REF_SWITCH = 39;
const int DI_40_Z_REF_SWITCH = 40;
const int DI_41_SPINDLE_ROTATION = 41;
const int DI_42_SCREW_READY = 42;  // Screw present in pawl
const int DI_43_SCREW_IN_SEPARATOR = 43;  // Screw present in separator (rosa)
const int DI_44_SEPARATOR_IN_STARTING_POSITION = 44;  // Separator in incoming position (rot)
const int DI_45_SEPARATOR_IN_WORKING_POSITION = 45;  // Separator in output position (grau-rosa)
const int DI_46_PIN = 46;
const int DI_47_PIN = 47;
const int DI_48_PIN = 48;
const int DI_49_PIN = 49;
const int DI_50_PIN = 50;
const int DI_51_PIN = 51;
const int DI_52_EMERGENCY_BUTTON = 52;  // Emergency Stop Button
const int DI_53_START_BUTTON = 53; // Start Button

// General purpose 24V DC Digital Outputs (on the "Digital Output Board")--------------------
const int DO_22_SCREW_SEPARATOR = 22;  // Separator Cylinder
const int DO_23_SCREW_INJECTOR = 23;  // Srewc injector air
const int DO_24_BLOW_OFF_NOZZLE = 24;  // Blow off nozzle in screw feeder
const int DO_25_PIN = 25;  // Res. Output
const int DO_26_SCREW_FEEDER = 26;  // Screw feeder
const int DO_27_VACUUM = 27;  // Vacuum for Screw
const int DO_28_RELEASE = 28; // Screw releasing air
const int DO_29_PIN = 29;
const int DO_30_PIN = 30;
const int DO_31_PIN = 31;
const int DO_32_PIN = 32;
const int DO_33_PIN = 33;
const int DO_34_PIN = 34;
const int DO_35_PIN = 35;
const int DO_36_PIN = 36;
const int DO_37_PIN = 37;

// Stepper Pins (on the "Stepper Board")---------------------------------------------------
// The X stepper pins
const int STEPPER_X_STEP_PIN = 13;
const int STEPPER_X_DIR_PIN = 14;
const int STEPPER_X_CURRENT_PIN = 5;

// The Y stepper pins
const int STEPPER_Y_STEP_PIN = 12;
const int STEPPER_Y_DIR_PIN = 15;
const int STEPPER_Y_CURRENT_PIN = 4;

// The Z stepper pins
const int STEPPER_Z_STEP_PIN = 11;
const int STEPPER_Z_DIR_PIN = 16;
const int STEPPER_Z_CURRENT_PIN = 3;

// The A stepper pins
const int STEPPER_A_STEP_PIN = 10;
const int STEPPER_A_DIR_PIN = 17;
const int STEPPER_A_CURRENT_PIN = 2;

// Define some steppers and the pins they will use
AccelStepper stepperX(AccelStepper::DRIVER, STEPPER_X_STEP_PIN, STEPPER_X_DIR_PIN);
AccelStepper stepperY(AccelStepper::DRIVER, STEPPER_Y_STEP_PIN, STEPPER_Y_DIR_PIN);
AccelStepper stepperZ(AccelStepper::DRIVER, STEPPER_Z_STEP_PIN, STEPPER_Z_DIR_PIN);
AccelStepper stepperA(AccelStepper::DRIVER, STEPPER_A_STEP_PIN, STEPPER_A_DIR_PIN);

// Axis calibration (stepper motor "steps" per mm)
float stepsPerMmX = 25; // 12.5 for GT2, Z16 (10.2mm pitch diameter) and 1/2 step (400 steps/Rev.)
float stepsPerMmY = 25; // 25 for 1/4 step (800 steps/Rev.)
float stepsPerMmZ = 25;
float stepsPerRoundA = 800;

// Accelerations for normal operation
float accelX = 40000.0; //40000
float accelY = 40000.0; //40000
float accelZ = 40000.0; // Z & A axis acceleration MUST BE IDENTICAL!
float accelA = 40000.0; // about 40000 for good screwing results

// X, Y, Z axis current
int currentX = 100;
int currentY = 100;
int currentZ = 150;

// A axis torque (current) calibration
// PWM signal, 255 = always on, 127 = 50%, filtered with RC-filter for analog voltage signal to TMC2100 driver
int currentA = 150; // 150 = 30Ncm @ 400 RPM (with TMC2100)

// Define Z Axis variables
float zError;
float zRetract;
float zSuck;
float zScrewBegin;
float zScrewingDepth; // how deep is the screw screwed in (+ about 3mm reserve)?

// Define screw pitch
float screwPitch;

// Define screw RPM
int screwRpm;
boolean spindleWasAtFullRpm = false;
boolean spindleStalled = false;
boolean stallDetectionActive = false;

// Define screw feeder variables
boolean screwRequest = false;
boolean screwIsFeeding = false;

// Define max. stepper speeds
float homingSpeed = 1500;
float homingRetractSpeed = 200;
float maxSpeed = 7000;  // 7000
float maxSpeedSucked = 5000;

// The currerntly processed screw in the pattern
unsigned int screwNo = 0;

// How many screws are in the selected pattern?
unsigned int numberOfScrews;

// The currently active program
unsigned int activeProgram = 1;

// The max. number of programs
const unsigned int numberOfPrograms = 20;

// Has the operation mode (Run, Stop etc.) changed?
boolean modeDidChange = false;

// The measured spindle rotation count
volatile long spindleDegreesRaw = 0; // Sensor state changes (impulses)
volatile long spindleRpmRaw = 0;  // "volatile" is required because of the interrupt function!
float spindleDegrees = 0; // in degrees

// Tolerances for screwing angle monitoring
int spindleDegreesMin = 0; // in degrees
int spindleDegreesMax = 0; // in degrees
boolean error = false;
unsigned long rpm = 0; // the measured live spindle RPM

unsigned int operationMode = 1; // operationMode: 0 = Run, 1 = Stop, 2 = Reset, 3 = Program Select 4 = Axis homing

boolean ProgNoInput = false;

// Was the emegrency stop button pressed?
boolean emergencyWasPressed = false;

// Create cylinder position monitoring objects (one for each cylinder)
cylinderPosition separatorMonitoring;

// the currently displayed error message number
int currentMessage = 999;

boolean repeated = false; // Was the screw injection pulse already repeated?

// Timer
SimpleTimer timer;

//
// =======================================================================================================
// TABS FOR SCREW PATTERN SPECIFICATION (Edit them for implementing new types)
// =======================================================================================================
//

#include "patterns.h" // "Screw patterns"
#include "typeVariables.h" // Z axis heihgts, spindle RPM, screw pitch etc.
#include "offsets.h" // Axis offsets for each screw pattern

//
// =======================================================================================================
// READ GENERAL PURPOSE INPUTS
// =======================================================================================================
//

boolean refSwitchX() {
  return digitalRead(DI_38_X_REF_SWITCH);
}

boolean refSwitchY() {
  return digitalRead(DI_39_Y_REF_SWITCH);
}

boolean refSwitchZ() {
  return digitalRead(DI_40_Z_REF_SWITCH);
}

// Pin 41 is an interrupt-Pin

boolean screwReady() {
  return digitalRead(DI_42_SCREW_READY);
}

boolean screwInSeparator() {
  return digitalRead(DI_43_SCREW_IN_SEPARATOR);
}

boolean separatorInStartingPosition() {
  return digitalRead(DI_44_SEPARATOR_IN_STARTING_POSITION);
}

boolean separatorInWorkingPosition() {
  return digitalRead(DI_45_SEPARATOR_IN_WORKING_POSITION);
}

boolean emergencyStop() {
  return digitalRead(DI_52_EMERGENCY_BUTTON);
}


//
// =======================================================================================================
// MAIN ARDUINO SETUP (1x during startup)
// =======================================================================================================
//

void setup()
{

  // I2C initialization-------------------------------------
  Wire.setClock(100000); // Set 100kHz I2C clock for the PCF8574

  // Serial initialization----------------------------------
  //#ifdef DEBUG
  Serial.begin(115200);
  //#endif

  // Keypad--------------------------------------------------
  customKeypad.setHoldTime(250);       // Default is 1000mS
  customKeypad.setDebounceTime(50);    // Default is 50mS

  // SD card initialization-----------------------------------
  pinMode(SD_CS, OUTPUT);

  Serial.print("Initializing SD card... ");

  // see if the card is present and can be initialized:
  if (!SD.begin(SD_CS)) {
    Serial.println("Card failed or not present");
    // don't do anything more:
  } else {
    Serial.println("Card initialized.");
  }

  // Stepper Pins--------------------------------------------
  pinMode(STEPPER_X_STEP_PIN, OUTPUT);
  pinMode(STEPPER_X_DIR_PIN, OUTPUT);
  pinMode(STEPPER_X_CURRENT_PIN, OUTPUT);
  pinMode(STEPPER_Y_STEP_PIN, OUTPUT);
  pinMode(STEPPER_Y_DIR_PIN, OUTPUT);
  pinMode(STEPPER_Y_CURRENT_PIN, OUTPUT);
  pinMode(STEPPER_Z_STEP_PIN, OUTPUT);
  pinMode(STEPPER_Z_DIR_PIN, OUTPUT);
  pinMode(STEPPER_Z_CURRENT_PIN, OUTPUT);
  pinMode(STEPPER_A_STEP_PIN, OUTPUT);
  pinMode(STEPPER_A_DIR_PIN, OUTPUT);
  pinMode(STEPPER_A_CURRENT_PIN, OUTPUT);

  // General Purpose 24V DC Inputs---------------------------
  pinMode(DI_38_X_REF_SWITCH, INPUT);
  pinMode(DI_39_Y_REF_SWITCH, INPUT);
  pinMode(DI_40_Z_REF_SWITCH, INPUT);
  pinMode(DI_41_SPINDLE_ROTATION, INPUT);
  attachInterrupt(digitalPinToInterrupt(DI_41_SPINDLE_ROTATION), rotationInterrupt, CHANGE);
  pinMode(DI_42_SCREW_READY, INPUT);
  pinMode(DI_43_SCREW_IN_SEPARATOR, INPUT);
  pinMode(DI_44_SEPARATOR_IN_STARTING_POSITION, INPUT);
  pinMode(DI_45_SEPARATOR_IN_WORKING_POSITION, INPUT);
  pinMode(DI_46_PIN, INPUT);
  pinMode(DI_47_PIN, INPUT);
  pinMode(DI_48_PIN, INPUT);
  pinMode(DI_49_PIN, INPUT);
  pinMode(DI_50_PIN, INPUT);
  pinMode(DI_51_PIN, INPUT);
  pinMode(DI_52_EMERGENCY_BUTTON, INPUT);
  pinMode(DI_53_START_BUTTON, INPUT);

  // General Purpose 24V DC Outputs---------------------------
  pinMode(DO_22_SCREW_SEPARATOR, OUTPUT);
  pinMode(DO_23_SCREW_INJECTOR, OUTPUT);
  pinMode(DO_24_BLOW_OFF_NOZZLE, OUTPUT);
  pinMode(DO_25_PIN, OUTPUT);
  pinMode(DO_26_SCREW_FEEDER, OUTPUT);
  pinMode(DO_27_VACUUM, OUTPUT);
  pinMode(DO_28_RELEASE, OUTPUT);
  pinMode(DO_29_PIN, OUTPUT);
  pinMode(DO_30_PIN, OUTPUT);
  pinMode(DO_31_PIN, OUTPUT);
  pinMode(DO_32_PIN, OUTPUT);
  pinMode(DO_33_PIN, OUTPUT);
  pinMode(DO_34_PIN, OUTPUT);
  pinMode(DO_35_PIN, OUTPUT);
  pinMode(DO_36_PIN, OUTPUT);
  pinMode(DO_37_PIN, OUTPUT);

  // Initialize outputs
  digitalWrite(DO_22_SCREW_SEPARATOR, LOW);
  digitalWrite(DO_23_SCREW_INJECTOR, LOW);
  digitalWrite(DO_24_BLOW_OFF_NOZZLE, LOW);
  digitalWrite(DO_25_PIN, LOW);
  digitalWrite(DO_26_SCREW_FEEDER, LOW);
  digitalWrite(DO_27_VACUUM, LOW);
  digitalWrite(DO_28_RELEASE, LOW);


  // Adjust the current for each axis
  analogWrite(STEPPER_X_CURRENT_PIN, currentX);  //255 = 1/2 of 3.3V (Arduino DUE) = 1.65A
  analogWrite(STEPPER_Y_CURRENT_PIN, currentY);
  analogWrite(STEPPER_Z_CURRENT_PIN, currentZ);
  analogWrite(STEPPER_A_CURRENT_PIN, 5); // screwing torque is written in robot FSM!


  // NOTE: the max. stepping frequency (in total for all motors) is 4000 steps/s!!(on a Due 14000)--------------------------

  // Drive Z axis to zero
  stepperZ.setMaxSpeed(homingSpeed); // @4000: 400 Steps per Rev. (1/2 Step Mode) = 10 Rev./s = 600 RPM (571 measured)
  stepperZ.setAcceleration(65000.0);  // fast accelerations are needed for homing!
  stepperZ.moveTo(0);

  // Drive X & Y axis to zero
  stepperX.setMaxSpeed(homingSpeed);
  stepperX.setAcceleration(65000.0);  // 50000 max. for 1/2 steps
  stepperX.moveTo(0);

  stepperY.setMaxSpeed(homingSpeed);
  stepperY.setAcceleration(65000.0);
  stepperY.moveTo(0);

  stepperA.setAcceleration(65000.0);

  // LCD initialization
  delay(1000);
  lcd.init(); // Windows = .begin, OS X = .init !!
  lcd.backlight();
  lcd.clear();
  lcd.setCursor(3, 0);
  lcd.print("Welcome To");
  lcd.setCursor(1, 1);
  lcd.print("Screw-O-Matic");
  delay(1500);

  homingCycle();  // execute automatic axis homing cycle

  // adjust axis accelerations for normal operation
  stepperX.setAcceleration(accelX);
  stepperY.setAcceleration(accelY);
  stepperZ.setAcceleration(accelZ);
  stepperA.setAcceleration(accelA);

  // Timer, which triggers the spindle RPM calculation every 60ms
  timer.setInterval(60, getSpindleRPM);

  // Start button reading timer
  timer.setInterval(20, readButtonFunction);
}

//
// =======================================================================================================
// MAIN LOOP
// =======================================================================================================
//

void loop()
{

  // Buttons
  //readButtonFunction();

  // Call Robot FSM
  fsmRobot();

  // Call screw feeder FSM
  fsmFeeder();

  // Call Feeder Relay ON / OFF function
  feederOnOff();

  // Screw ready for separating?
  screwReadyDetection();

  // Screw injection time limit
  screwInjectionTime();

  // Call Steppers
  stepperX.run();
  stepperY.run();
  stepperZ.run();
  stepperA.run();

  // refresh operation mode on display
  refreshMode();

  // Read Keypad
  readKeypad();

  // Error detection
  errorDetection();

  // Timer
  timer.run();
}

//
// =======================================================================================================
// HOMING CYCLE
// =======================================================================================================
//

int phase;

void homingCycle() {
  if (!emergencyStop()) { // if not emergency stop button pressed

    displayHoming(0); // Show Homing on Display

    // Z axis----------------------------------------------------------
    stepperZ.setMaxSpeed(homingSpeed);
    stepperZ.moveTo(1000 * stepsPerMmZ);  // max. seek distance 1000 mm
    while (!refSwitchZ()) stepperZ.run();   // until switch is ON
    stepperZ.stop(); // Stop as fast as possible: sets new target
    stepperZ.runToPosition();
    displayHoming(1);

    stepperZ.setMaxSpeed(homingRetractSpeed);
    stepperZ.move(-50 * stepsPerMmZ);    // go max. 50mm back
    while (refSwitchZ()) stepperZ.run();// until switch is released
    stepperZ.stop(); // Stop as fast as possible: sets new target
    stepperZ.runToPosition();

    stepperZ.setCurrentPosition(0); // Reset position to zero
    stepperZ.setMaxSpeed(maxSpeed); // switch back to full speed
    displayHoming(2);

    // Y axis----------------------------------------------------------
    stepperY.setMaxSpeed(homingSpeed);
    stepperY.moveTo(-1000 * stepsPerMmY);  // max. seek distance 1000 mm
    while (!refSwitchY()) stepperY.run();   // until switch is ON
    stepperY.stop(); // Stop as fast as possible: sets new target
    stepperY.runToPosition();
    displayHoming(3);

    stepperY.setMaxSpeed(homingRetractSpeed);
    stepperY.move(50 * stepsPerMmY);    // go max. 50mm back
    while (refSwitchY()) stepperY.run();// until switch is released
    stepperY.stop(); // Stop as fast as possible: sets new target
    stepperY.runToPosition();

    stepperY.setCurrentPosition(0); // Reset position to zero
    stepperY.setMaxSpeed(maxSpeed); // switch back to full speed
    displayHoming(4);

    // X axis----------------------------------------------------------
    stepperX.setMaxSpeed(homingSpeed);
    stepperX.moveTo(-1000 * stepsPerMmX);  // max. seek distance 1000 mm
    while (!refSwitchX()) stepperX.run();   // until switch is ON
    stepperX.stop(); // Stop as fast as possible: sets new target
    stepperX.runToPosition();
    displayHoming(5);

    stepperX.setMaxSpeed(homingRetractSpeed);
    stepperX.move(50 * stepsPerMmX);    // go max. 50mm back
    while (refSwitchX()) stepperX.run();// until switch is released
    stepperX.stop(); // Stop as fast as possible: sets new target
    stepperX.runToPosition();

    stepperX.setCurrentPosition(0); // Reset position to zero
    stepperX.setMaxSpeed(maxSpeed); // switch back to full speed!
    displayHoming(6);
    operationMode = 1; // 1 = Stop
    modeDidChange = true;
    //refreshMode();

    // Travel Y axis to front side-------------------------------------------
    stepperY.moveTo(165 * stepsPerMmY);
  }
  // Initialize Type Variables
  typeVariables();
}

//
// =======================================================================================================
// ROBOT FSM (Finite State Machine)
// =======================================================================================================
//
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

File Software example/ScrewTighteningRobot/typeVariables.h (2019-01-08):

//
// =======================================================================================================
// TYPE SPECIFIC Z AXIS VARIABLES, SCREW PITCH, SCREW RPM
// =======================================================================================================
//

void typeVariables() {
  switch (activeProgram) {
    case 1: // Program #1 (für Drehmoment Kalibrierung)
      // Define Z Axis heights
      zError = 75;
      zRetract = 20;
      zSuck = 20;
      zScrewBegin = -5.0;
      zScrewingDepth = 12.0;
      // Define number of screws in the pattern
      numberOfScrews = numberOfScrews1;
      // Define screw pitch
      screwPitch = 1.12;
      // Define screw RPM
      screwRpm = 400;
      // screwing rotation angle tolerances
      spindleDegreesMin = 0;
      spindleDegreesMax = 6000; // 6000° = limit inactive!
      break;

    case 2: // Program #2 
      // Define Z Axis heights
      zError = 100;
      zRetract = 50;
      zSuck = 20;
      zScrewBegin = -8.0;
      zScrewingDepth = 9.0;
      // Define number of screws in the pattern
      numberOfScrews = numberOfScrews2;
      // Define screw pitch
      screwPitch = 1.12;
      // Define screw RPM
      screwRpm = 400;
      // screwing rotation angle tolerances
      spindleDegreesMin = 800;
      spindleDegreesMax = 6000;
      break;

    case 3: // Program #3 
      // Define Z Axis heights
      zError = 100;
      zRetract = 50;
      zSuck = 20;
      zScrewBegin = -7.0;
      zScrewingDepth = 9.0;
      // Define number of screws in the pattern
      numberOfScrews = numberOfScrews3;
      // Define screw pitch
      screwPitch = 1.12;
      // Define screw RPM
      screwRpm = 400;
      // screwing rotation angle tolerances
      spindleDegreesMin = 800;
      spindleDegreesMax = 6000;
      break;

    case 4: // Program #4 
      // Define Z Axis heights
      zError = 100;
      zRetract = 50;
      zSuck = 20;
      zScrewBegin = -8.0;
      zScrewingDepth = 9.0;
      // Define number of screws in the pattern
      numberOfScrews = numberOfScrews4;
      // Define screw pitch
      screwPitch = 1.12;
      // Define screw RPM
      screwRpm = 400;
      // screwing rotation angle tolerances
      spindleDegreesMin = 800;
      spindleDegreesMax = 6000;
      break;

    case 5: // Program #5
      // Define Z Axis heights
      zError = 100;
      zRetract = 50;
      zSuck = 20;
      zScrewBegin = -8.0;
      zScrewingDepth = 9.0;
      // Define number of screws in the pattern
      numberOfScrews = numberOfScrews5;
      // Define screw pitch
      screwPitch = 1.12;
      // Define screw RPM
      screwRpm = 400;
      // screwing rotation angle tolerances
      spindleDegreesMin = 800;
      spindleDegreesMax = 6000;
      break;

    case 6: // Program #6
      // Define Z Axis heights
      zError = 100;
      zRetract = 50;
      zSuck = 20;
      zScrewBegin = -8.0;
      zScrewingDepth = 9.0;
      // Define number of screws in the pattern
      numberOfScrews = numberOfScrews6;
      // Define screw pitch
      screwPitch = 1.12;
      // Define screw RPM
      screwRpm = 400;
      // screwing rotation angle tolerances
      spindleDegreesMin = 800;
      spindleDegreesMax = 6000;
      break;

    case 7: // Program #7
      // Define Z Axis heights
      zError = 100;
      zRetract = 50;
      zSuck = 20;
      zScrewBegin = -8.0;
      zScrewingDepth = 9.0;
      // Define number of screws in the pattern
      numberOfScrews = numberOfScrews7;
      // Define screw pitch
      screwPitch = 1.12;
      // Define screw RPM
      screwRpm = 400;
      // screwing rotation angle tolerances
      spindleDegreesMin = 800;
      spindleDegreesMax = 6000;
      break;

    case 8: // Program #8
      // Define Z Axis heights
      zError = 100;
      zRetract = 50;
      zSuck = 20;
      zScrewBegin = -8.0;
      zScrewingDepth = 9.0;
      // Define number of screws in the pattern
      numberOfScrews = numberOfScrews8;
      // Define screw pitch
      screwPitch = 1.12;
      // Define screw RPM
      screwRpm = 400;
      // screwing rotation angle tolerances
      spindleDegreesMin = 800;
      spindleDegreesMax = 6000;
      break;

    case 9: // Program #9
      // Define Z Axis heights
      zError = 100;
      zRetract = 50;
      zSuck = 20;
      zScrewBegin = -8.0;
      zScrewingDepth = 9.0;
      // Define number of screws in the pattern
      numberOfScrews = numberOfScrews9;
      // Define screw pitch
      screwPitch = 1.12;
      // Define screw RPM
      screwRpm = 400;
      // screwing rotation angle tolerances
      spindleDegreesMin = 750;
      spindleDegreesMax = 6000;
      break;

    case 10: // Program #10
      // Define Z Axis heights
      zError = 100;
      zRetract = 50;
      zSuck = 20;
      zScrewBegin = -8.0;
      zScrewingDepth = 9.0;
      // Define number of screws in the pattern
      numberOfScrews = numberOfScrews10;
      // Define screw pitch
      screwPitch = 1.12;
      // Define screw RPM
      screwRpm = 400;
      // screwing rotation angle tolerances
      spindleDegreesMin = 800;
      spindleDegreesMax = 6000;
      break;

      case 11: // Program #11
      // Define Z Axis heights
      zError = 100;
      zRetract = 50;
      zSuck = 20;
      zScrewBegin = -8.0;
      zScrewingDepth = 9.0;
      // Define number of screws in the pattern
      numberOfScrews = numberOfScrews11;
      // Define screw pitch
      screwPitch = 1.12;
      // Define screw RPM
      screwRpm = 400;
      // screwing rotation angle tolerances
      spindleDegreesMin = 800;
      spindleDegreesMax = 6000;
      break;

      case 12: // Program #12
      // Define Z Axis heights
      zError = 100;
      zRetract = 50;
      zSuck = 20;
      zScrewBegin = -8.0;
      zScrewingDepth = 9.0;
      // Define number of screws in the pattern
      numberOfScrews = numberOfScrews12;
      // Define screw pitch
      screwPitch = 1.12;
      // Define screw RPM
      screwRpm = 400;
      // screwing rotation angle tolerances
      spindleDegreesMin = 800;
      spindleDegreesMax = 6000;
      break;

      case 13: // Program #13
      // Define Z Axis heights
      zError = 100;
      zRetract = 50;
      zSuck = 20;
      zScrewBegin = -7.0;
      zScrewingDepth = 9.0;
      // Define number of screws in the pattern
      numberOfScrews = numberOfScrews13;
      // Define screw pitch
      screwPitch = 1.12;
      // Define screw RPM
      screwRpm = 400;
      // screwing rotation angle tolerances
      spindleDegreesMin = 800;
      spindleDegreesMax = 6000;
      break;
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

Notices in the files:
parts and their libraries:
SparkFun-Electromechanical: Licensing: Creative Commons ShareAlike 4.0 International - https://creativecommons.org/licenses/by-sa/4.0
